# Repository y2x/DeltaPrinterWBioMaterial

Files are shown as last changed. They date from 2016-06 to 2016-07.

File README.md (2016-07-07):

# Delta 3D Printer With Bio-Material

## Video
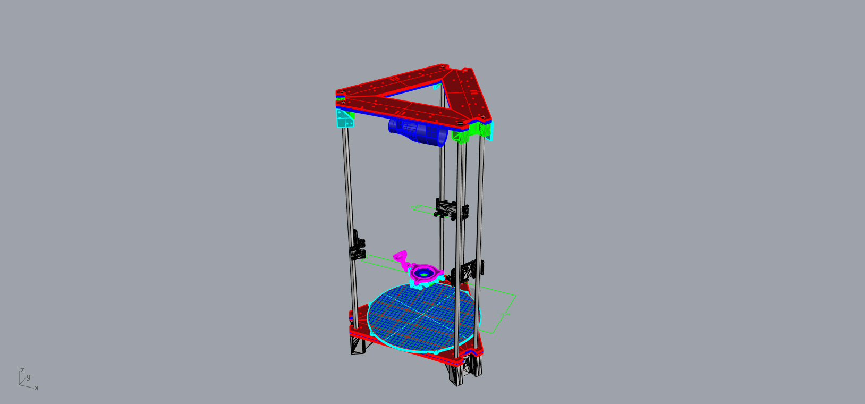
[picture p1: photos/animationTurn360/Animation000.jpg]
IMAGE ALT TEXT (https://youtu.be/-XNRGnteBmc)


## Description
This project is the continuation of Lorizio's :  *[`https://github.com/Lorizio/Delta-3D-Printer`](https://github.com/Lorizio/Delta-3D-Printer)*.
The main goal was to improve his existing printer and to be able to print different structures with home made materials.

## Construction
### Printed pieces :
- carriage : *[`http://www.thingiverse.com/thing:80425`](http://www.thingiverse.com/thing:80425)*
- idler end : *[`http://www.thingiverse.com/thing:143186`](http://www.thingiverse.com/thing:143186)*
- motor end : *[`http://www.thingiverse.com/thing:71687`](http://www.thingiverse.com/thing:71687)*
- platform : *[`http://www.thingiverse.com/thing:32850`](http://www.thingiverse.com/thing:32850)*
- ventilation : 
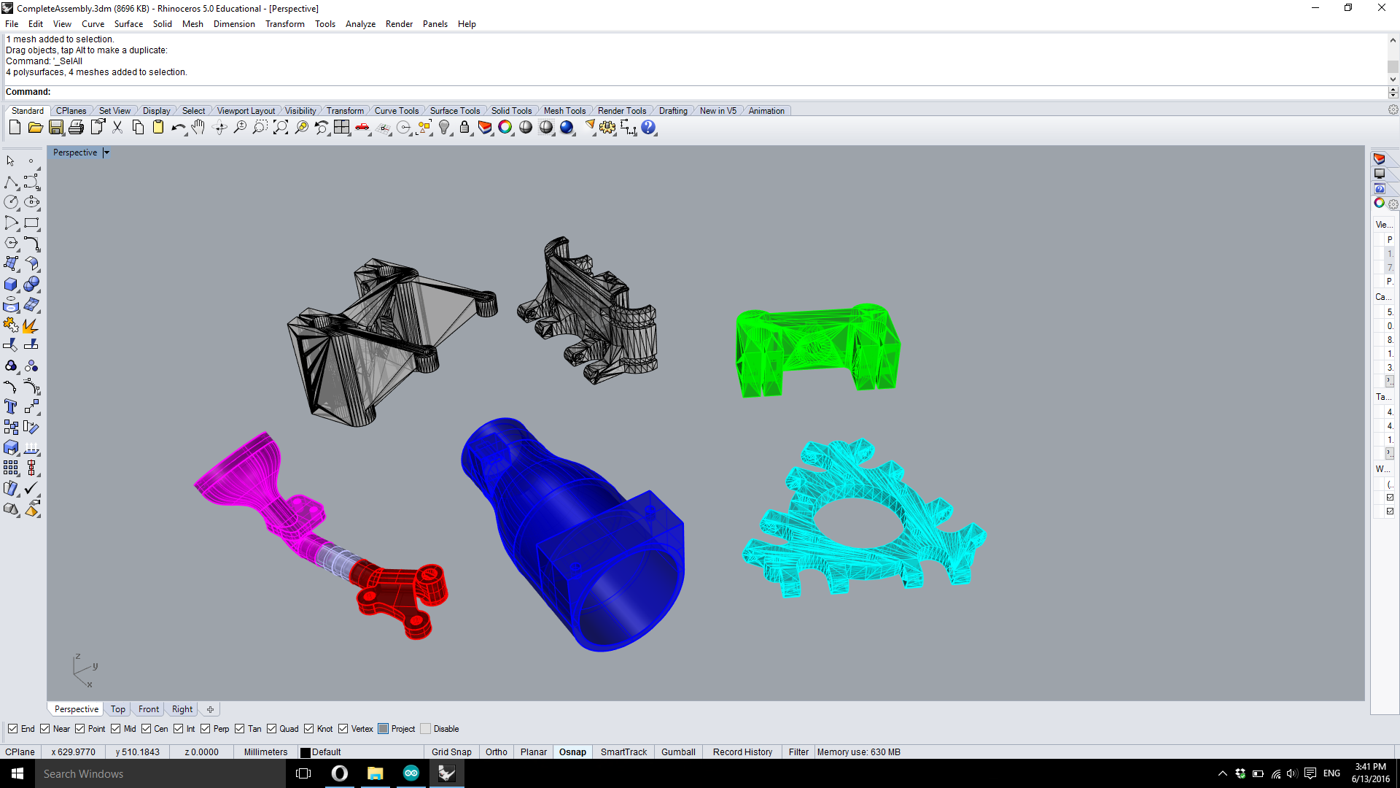
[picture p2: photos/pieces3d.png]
Printed pieces


### Laser-cut pieces for the frame:
- [Base assembly](hardware/baseAssembly.3dm)
- [Middle assembly](hardware/middleAssembly.3dm)
- [Top assembly](hardware/topAssembly.3dm)
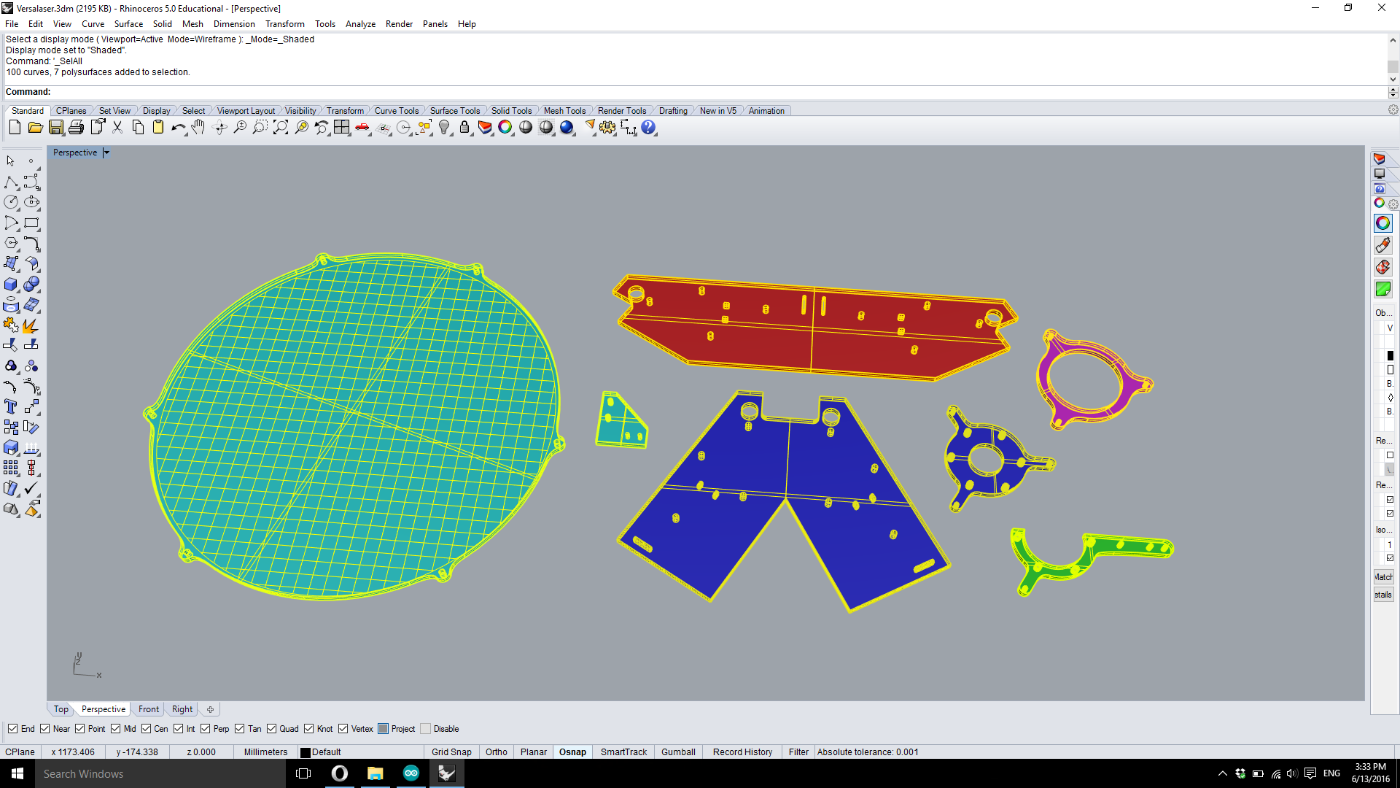
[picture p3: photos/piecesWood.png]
Wooden pieces


### Electronics & guiding
- [See the list](hardware/partsListToBuy.odt)

## Software & programs
### Arduino board
The actual prototype uses the [Marlin Firmware](https://github.com/MarlinFirmware/Marlin) which is widely used for custom 3D printer. The specifications are located in the configuration file in the marlin folder.
Here are the important sizing values :
```
  // Center-to-center distance of the holes in the diagonal push rods.
  #define DELTA_DIAGONAL_ROD 220.0 // mm

  // Horizontal offset from middle of printer to smooth rod center.
  #define DELTA_SMOOTH_ROD_OFFSET 178.0 // mm

  // Horizontal offset of the universal joints on the end effector.
  #define DELTA_EFFECTOR_OFFSET 33.5 // mm

  // Horizontal offset of the universal joints on the carriages.
  #define DELTA_CARRIAGE_OFFSET 28.0 // mm

  // Print surface diameter/2 minus unreachable space (avoid collisions with vertical towers).
  #define DELTA_PRINTABLE_RADIUS 90.0
```

### Slicer
The slicer was implemented using [Grasshopper3D](http://www.grasshopper3d.com/) on [Rhino3D](http://www.rhino3d.com/). It generates point from (almost) any brep surface and applies different transformations to the models to print interesting structures. Main features are to add zigzags (horizontally and vertically) change the layer height and the speed.
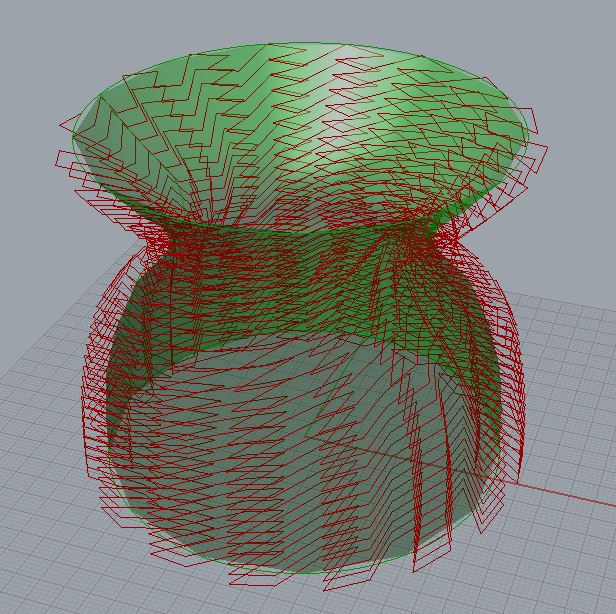
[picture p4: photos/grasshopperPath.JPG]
model in green, generated path in red


### Printed results
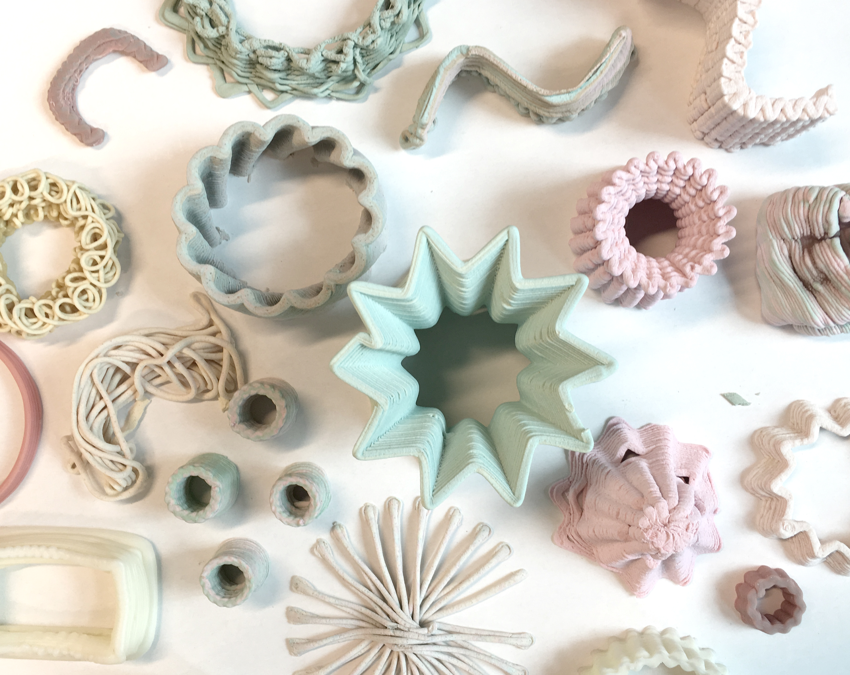
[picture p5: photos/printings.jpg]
printed results


### Authors
* **Philippe Heer** - *IC Master student*
* **Leonardo Wirz** - *IC Bachelor student*
* **Yuan Wang-Shih** - *Supervisor*
* **Huang Jeffrey** - *Professor*

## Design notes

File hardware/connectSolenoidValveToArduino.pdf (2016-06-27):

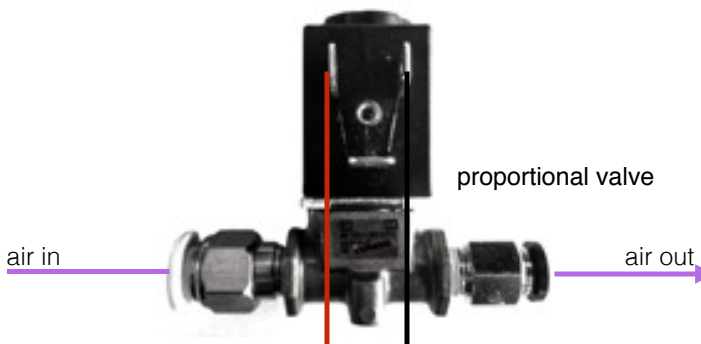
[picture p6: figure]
proportional valve; air in; air out
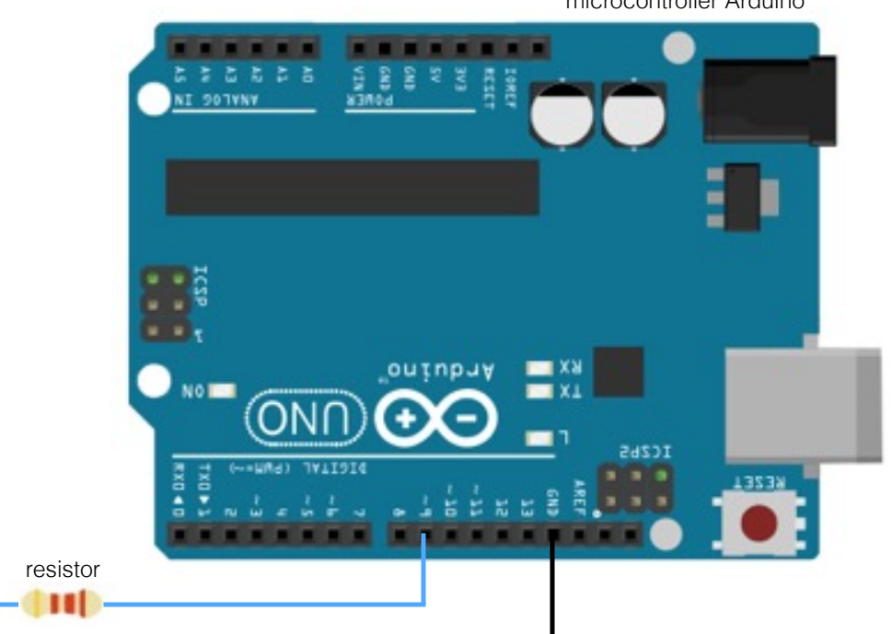
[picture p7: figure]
resistor

microcontroller Arduino

24V +

24V -

transistor

diode

#define valvePin 9

void setup() {
// put your setup code here, to run once: pinMode(valvePin, OUTPUT);

}

void loop() {

// put your main code here, to run repeatedly: analogWrite(valvePin, 170);
delay(15);

}

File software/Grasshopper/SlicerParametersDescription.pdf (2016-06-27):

Slicer parameters description

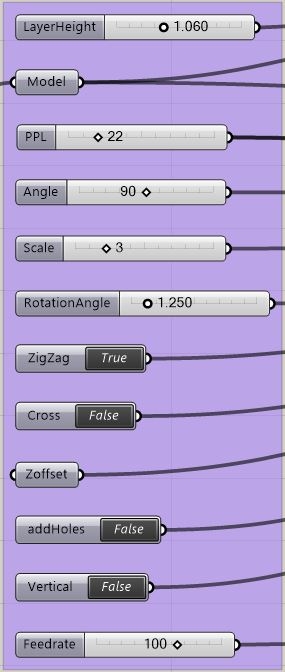
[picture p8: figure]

LayerHeight : set the layer height in millimeters between 0.5 and 2.

PPL : set the numbers of points per layers.

Angle : change the angle for the zigzag and crossed zigzag.

Scale : multiply the length of each line of the zigzag.

Rotation angle : twist the object, every layer rotates that angle in degrees.

ZigZag : enable zigzag.

Cross : enable crossed zigzag (only if zigzag is enabled).

Zoffset : shift the object in the z axis in millimeters.

AddHoles : removes certain points to create the hole effect.

Vertical : add a vetical zigzag.

Feedrate : set the speed printing, 60 = 1mm/s

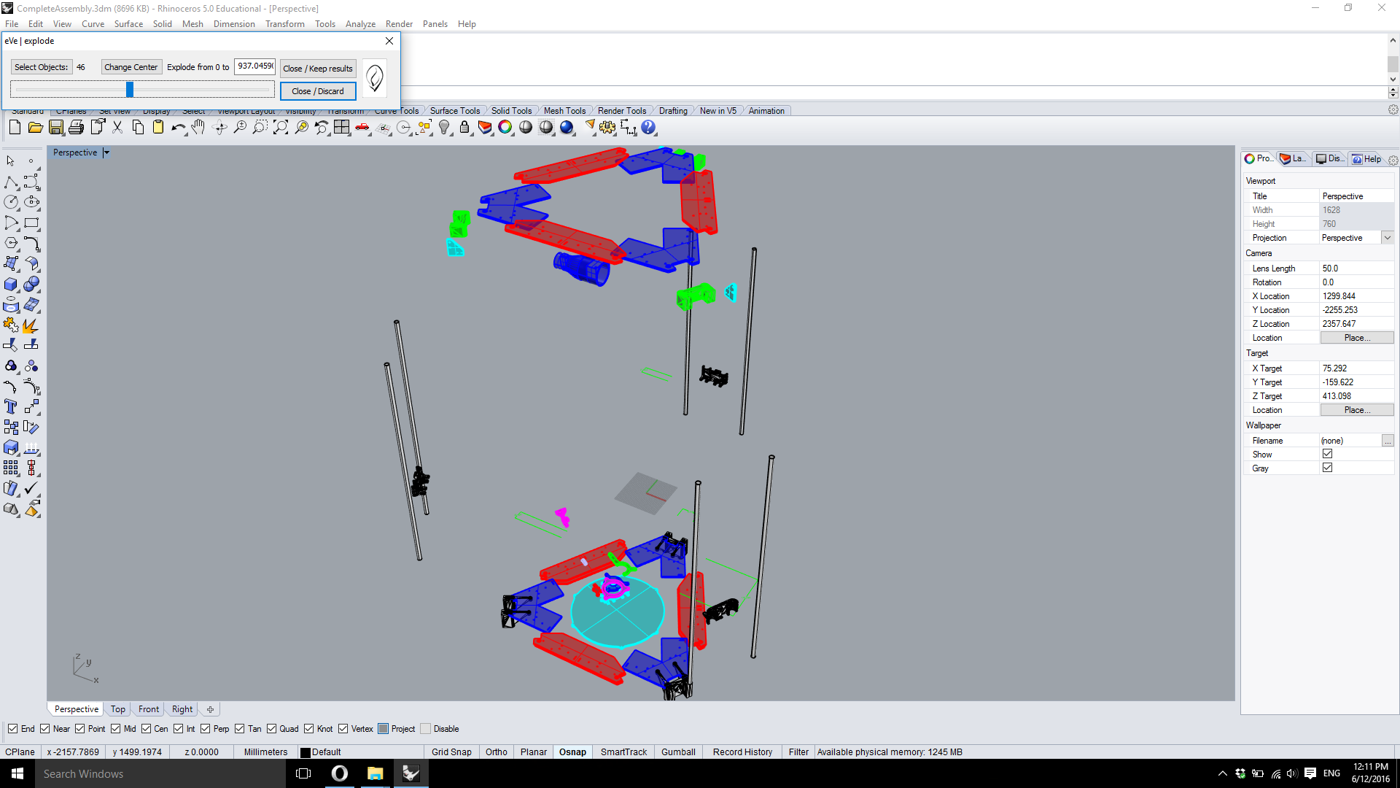
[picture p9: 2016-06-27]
photos/animationExplode/Screenshot (27).png

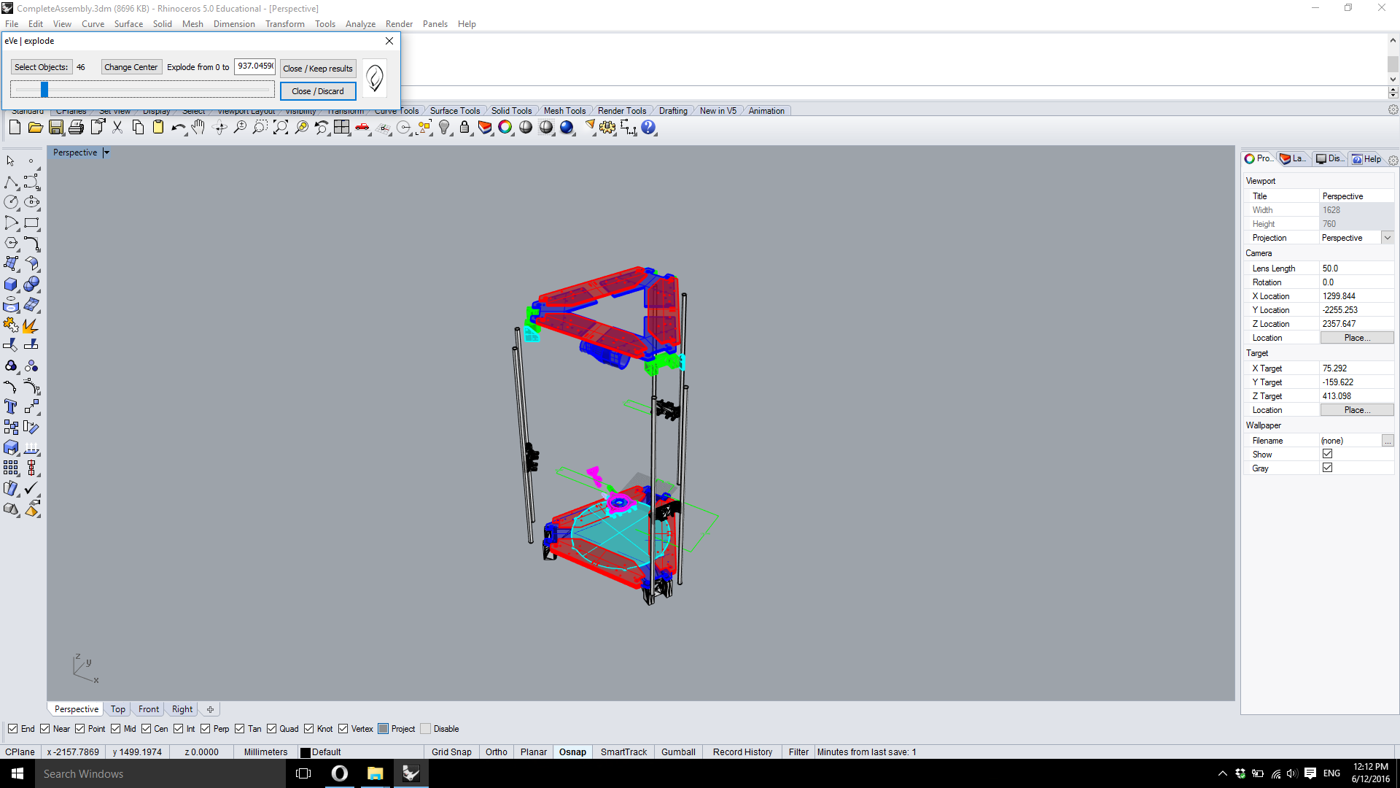
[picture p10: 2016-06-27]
photos/animationExplode/Screenshot (62).png

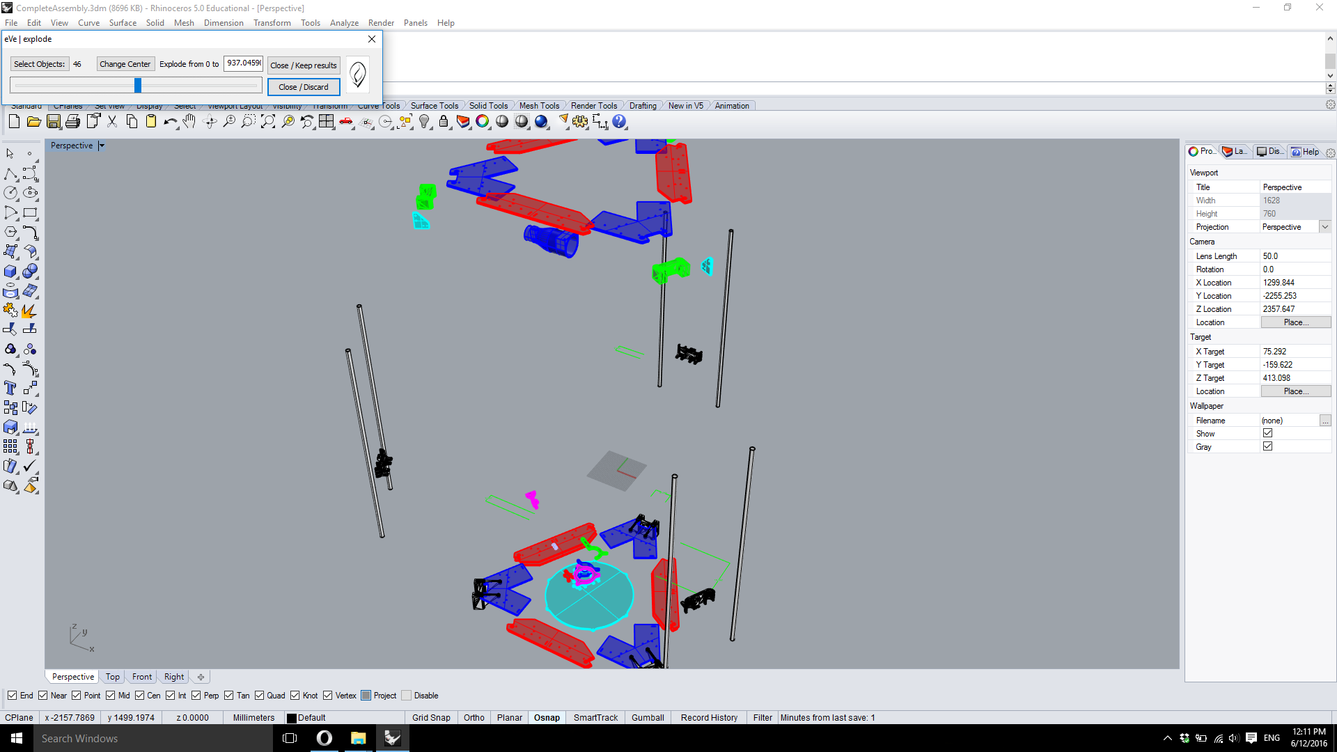
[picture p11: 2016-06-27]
photos/animationExplode/Screenshot (21).png

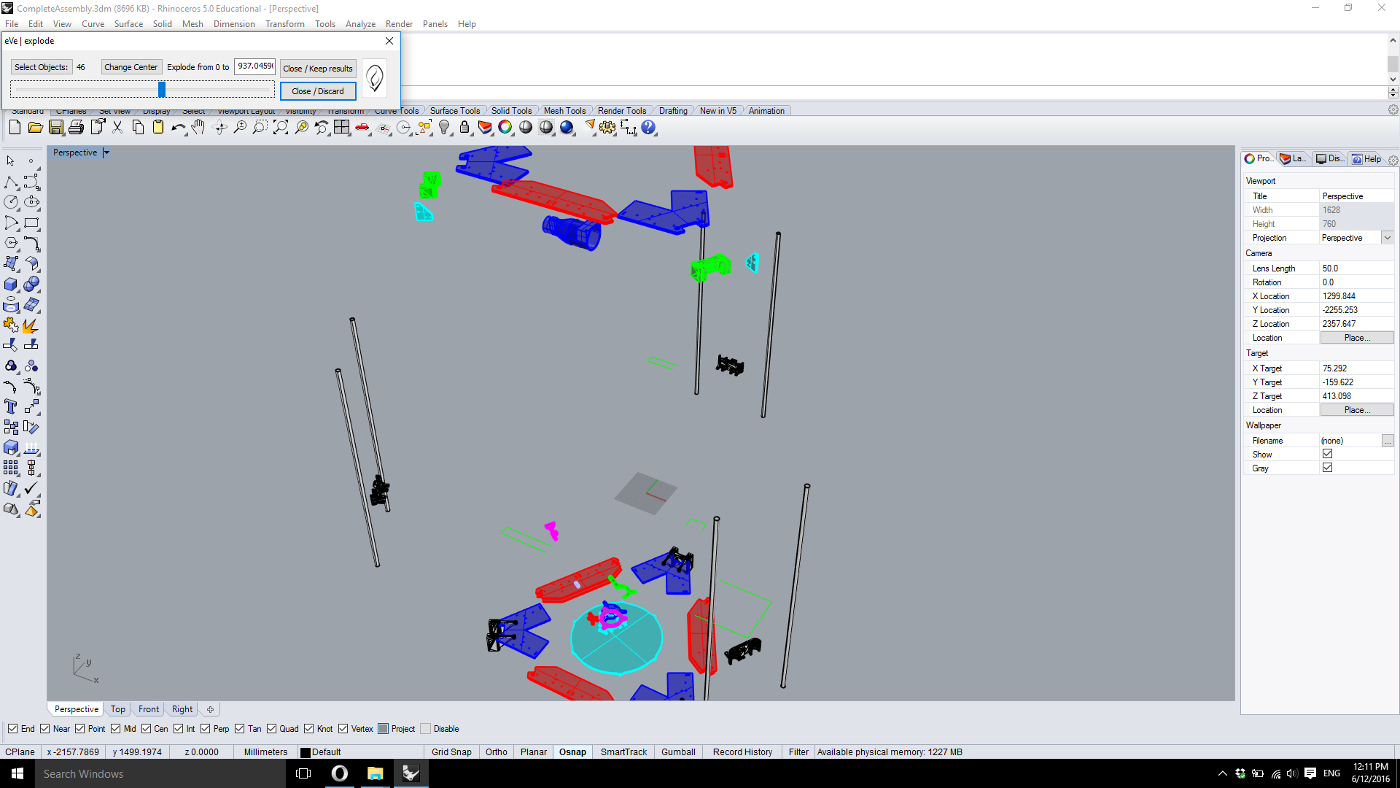
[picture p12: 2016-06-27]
photos/animationExplode/Screenshot (14).png

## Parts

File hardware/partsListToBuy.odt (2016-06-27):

You will need an air compressor machine accurate enough to control the pressure efficiently.

Structure parts :

High torque hybrid (3x)

http://www.zappautomation.co.uk/sy42sth47-1684a-high-torque-hybrid-stepper-motors.html

12mm steel rods (6x)

http://www.zappautomation.co.uk/sfc12-precision-round-rail.html

12 mm linear bearing (6x)

They need to slide along the steel rods smoothly

http://www.zappautomation.co.uk/lm10uu-linear-bearing-29451.html

GT2 belts (3x)

http://www.amazon.com/3DMakerWorld-GT2-Timing-Belt/dp/B00IDCG6ZU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

Traxxas 5347 with hollows balls (12x)

They must fit in the brass tube below. Two per tube.

http://www.amazon.com/Traxxas-5347-Hollow-Balls-Large/dp/B000BOLVJY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

Brass tube 8mm (6x)

Two tubes per axis. 23 centimeters each. The material doesn’t matter as long as it is solid and that the traxxas pieces can fit inside.

http://www.amazon.com/Engineering-Round-Brass-Tube-45/dp/B005WPASOG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

xbox 360 203W power brick 220V

http://www.amazon.co.uk/OFFICIAL-MICROSOFT-REPLACEMENT-POWER-SUPPLY/dp/B00AUYDF6M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

Some MDF panels of at least 12 mm.

Electronic part

Ultra Set (1x)

It comes with wires and all the required electronic components

https://gadgets3d.eu/index.php?route=product/product&product_id=70

Extruder parts

Glue Liquid Cartridge Dispenser Syringe Barrel 300CC Clear Black

http://www.amazon.co.uk/Liquid-Cartridge-Dispenser-Syringe-Barrel/dp/B00GMW4EBG

tips

http://www.adhesivedispensers.co.uk/TE714025PK.htm

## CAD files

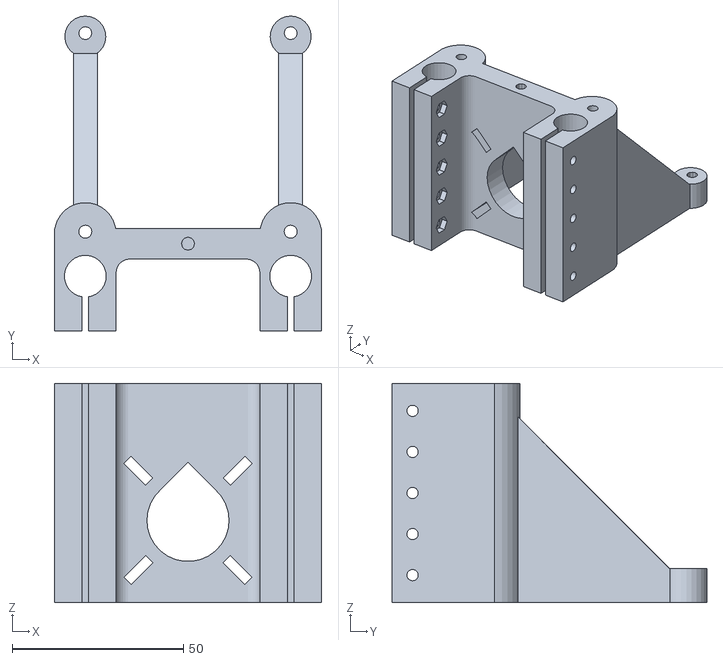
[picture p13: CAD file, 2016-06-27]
hardware/motor_end.stl
78.0 x 92.0 x 64.0

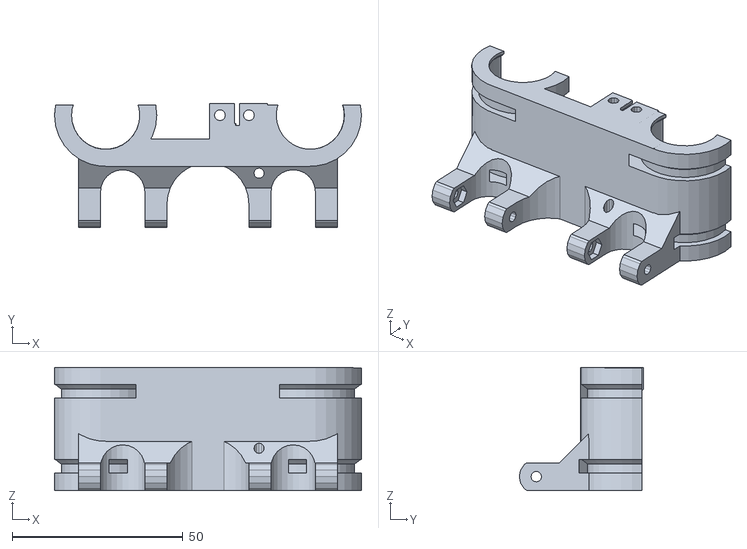
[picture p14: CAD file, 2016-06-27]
hardware/carriage-V1.2.stl
90.0 x 36.5 x 36.1

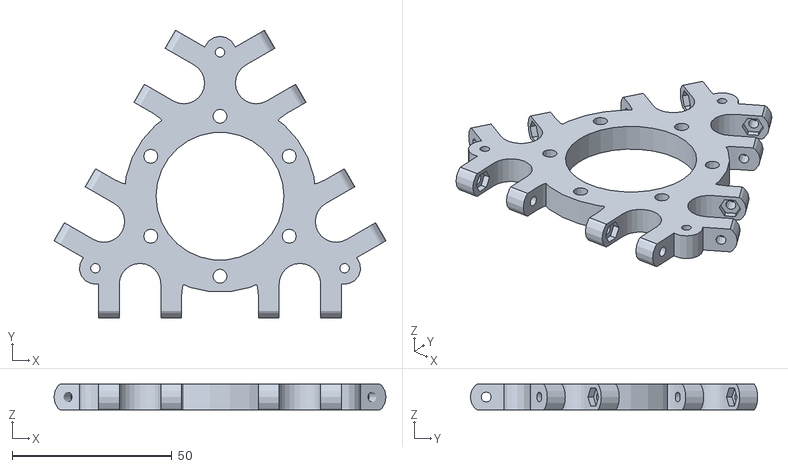
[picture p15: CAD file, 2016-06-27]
hardware/platform.stl
103.8 x 89.9 x 8.00

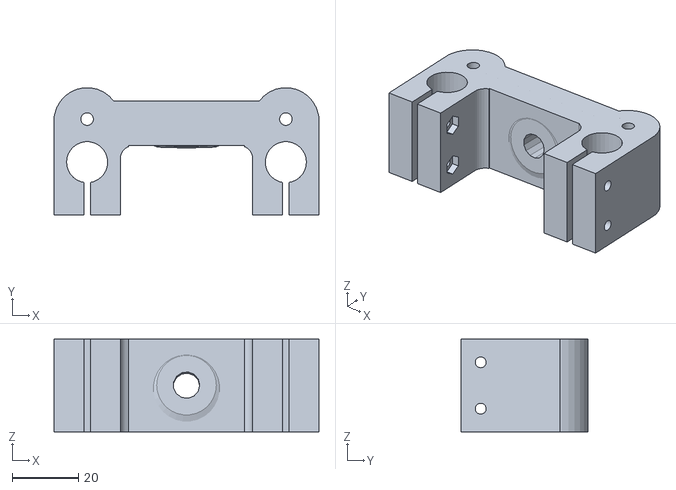
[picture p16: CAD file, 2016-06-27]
hardware/idler_end_V1.2.stl
80.0 x 38.4 x 28.0

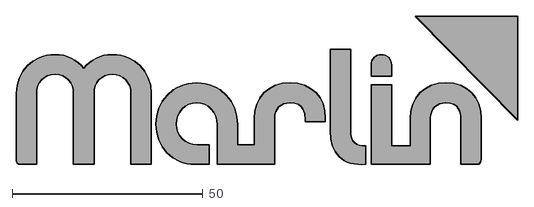
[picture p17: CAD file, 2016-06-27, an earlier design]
software/Arduino/Marlin-RC/Documentation/Logo/Marlin Logo_old.dxf
131.6 x 39.5

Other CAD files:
hardware/baseAssembly.3dm
hardware/middleAssembly.3dm
hardware/topAssembly.3dm

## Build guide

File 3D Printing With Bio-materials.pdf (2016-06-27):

by L. Wirz, P. Heer
Supervisor Y. Wang
Professor J. Huang

## 3D Printing With Bio-materials

### Outline

- Goal
- Hardware
- Software
- Material
- Issues

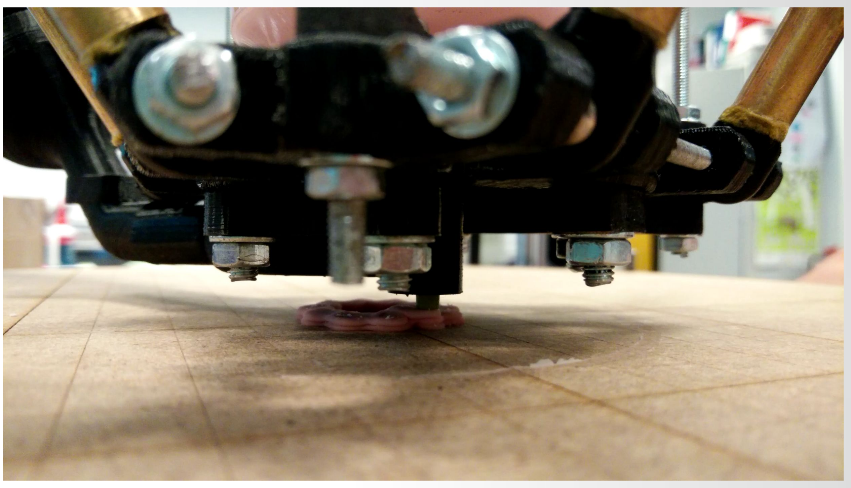
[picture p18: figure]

- Further development
- Demo

### Goal

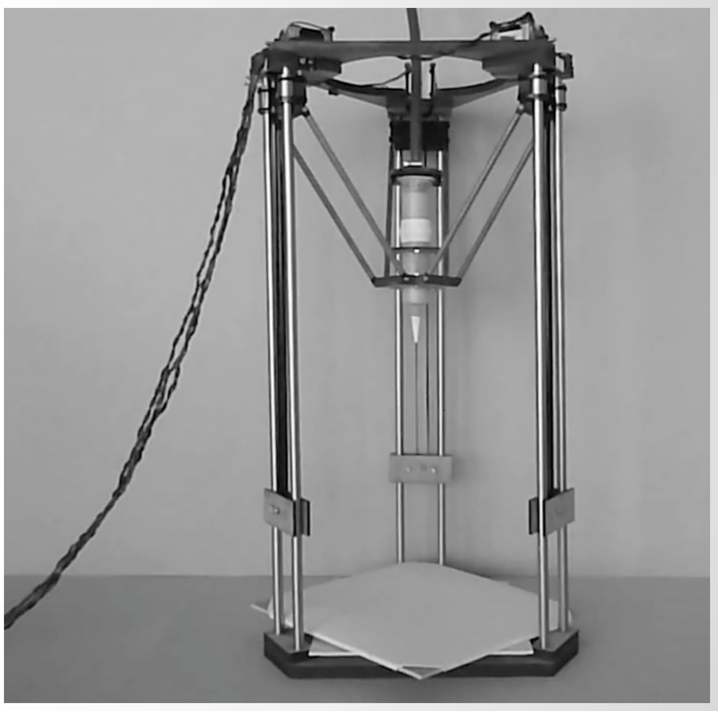
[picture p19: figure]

- improve existing printer
- new materials
- print different textures

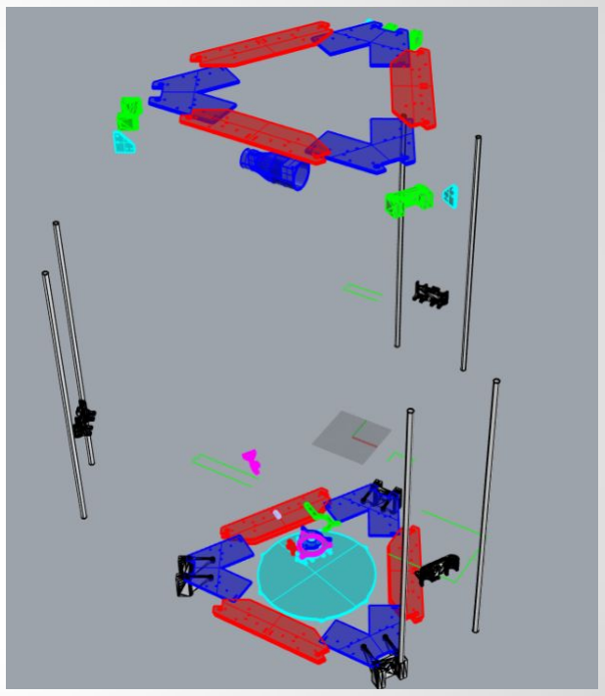
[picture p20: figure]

### Hardware

- Motors and sensors
- Air compressor
- Design with Rhino 5.0
- Cut with Versalaser
- Print with Makerbot Mini

### Wooden pieces

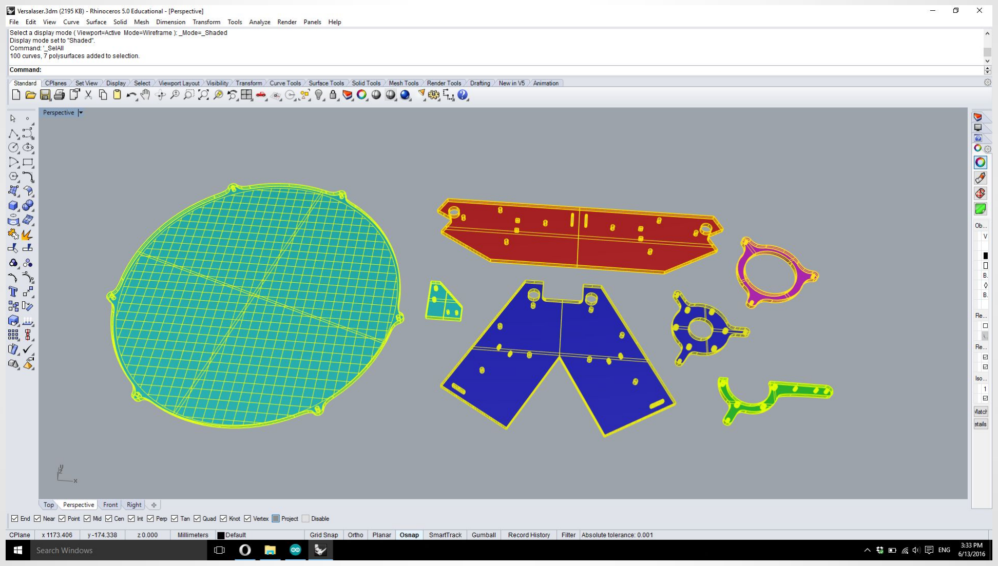
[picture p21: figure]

### 3d printed pieces

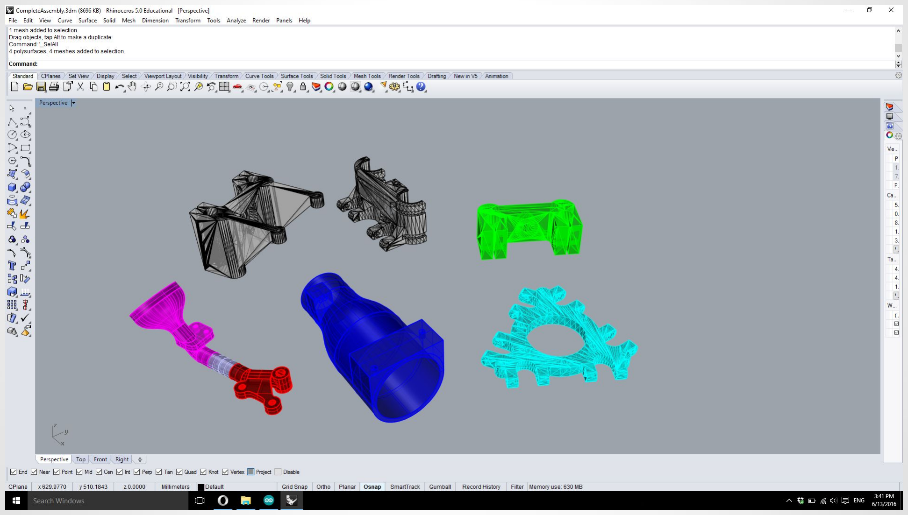
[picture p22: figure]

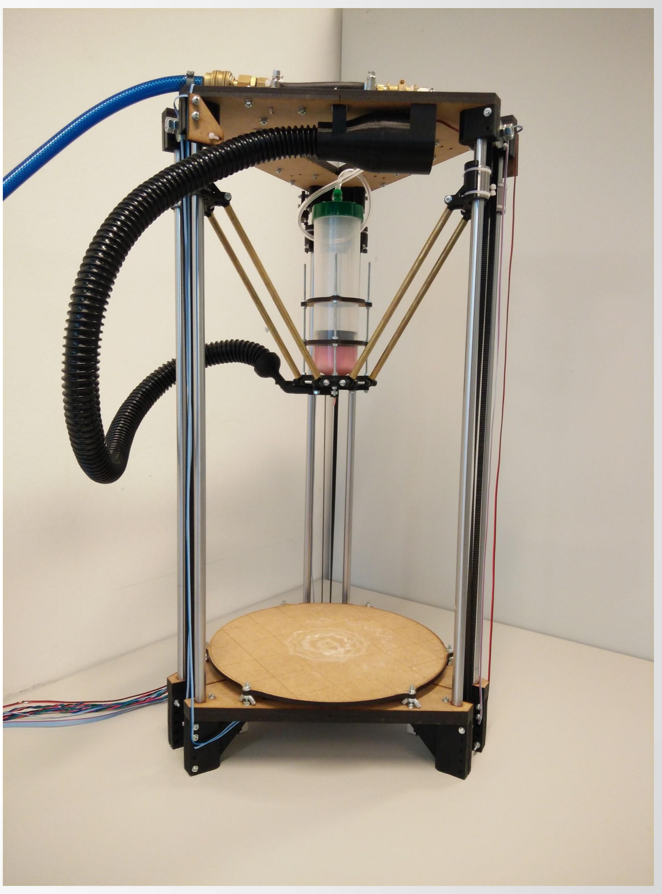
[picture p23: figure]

### Specifications

- diameter: 18cm
- height: 31cm
- speed: 1-2mm/s
- precision: 0.2mm
- pressure: 4 bar

### Material

- 100ml glue, 100g Maizena
- 4 spoons flour, 2 or 1 spoons salt and some water
- Food coloring

### Software

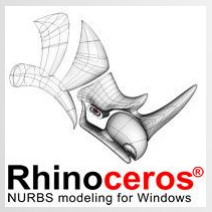
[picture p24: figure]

- Rhino 5.0

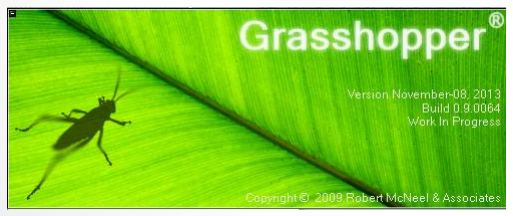
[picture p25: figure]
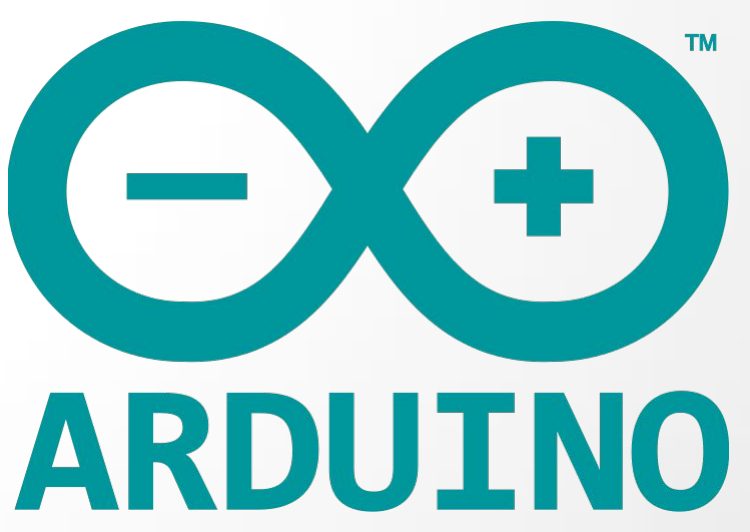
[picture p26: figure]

- Grasshopper (plugin of Rhino)
- Arduino Marlin RC software

### Custom slicer

- Create different paths and textures
- Zigzag (horizontal / vertical / alternating / angle)
- Speed variable
- Layer height, layer offset

### Slicer interface

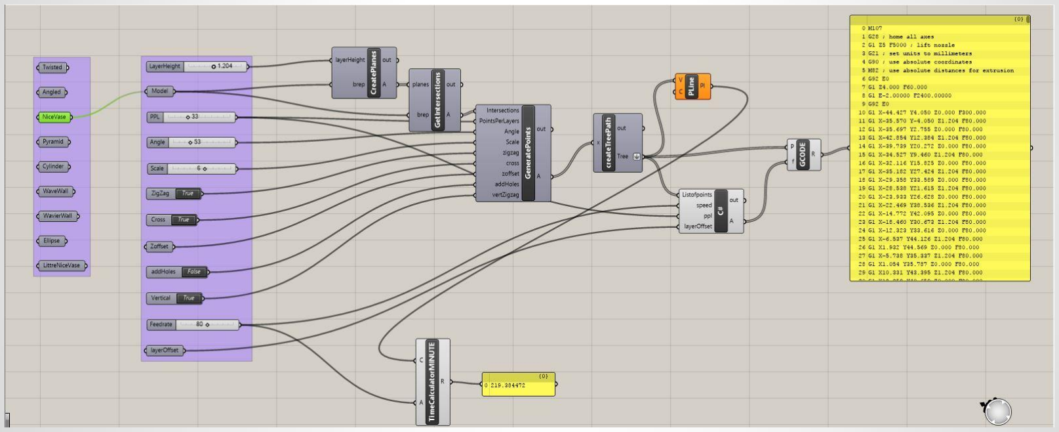
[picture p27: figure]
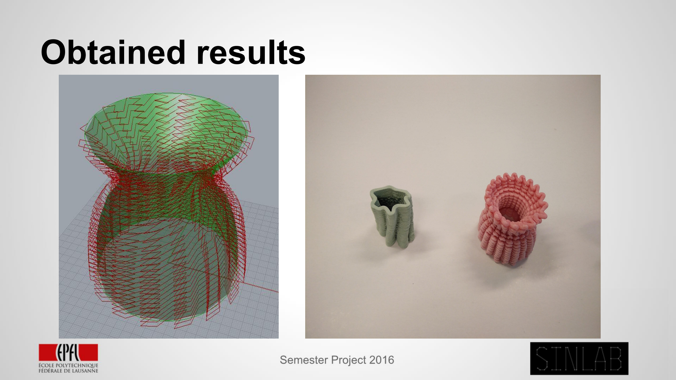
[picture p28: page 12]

### Obtained results

### Issues

- Makerbot Mini
- Printer calibration
- Material (2 different recipes)
- Printtime

### Further development

- Use other extruders
- Other materials

### Demo

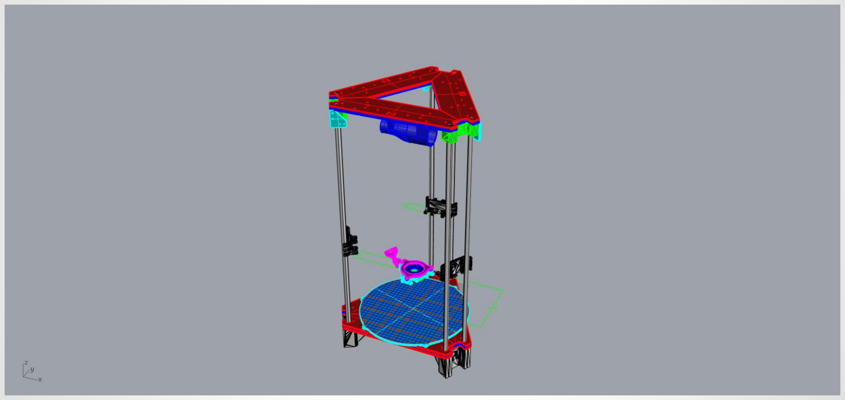
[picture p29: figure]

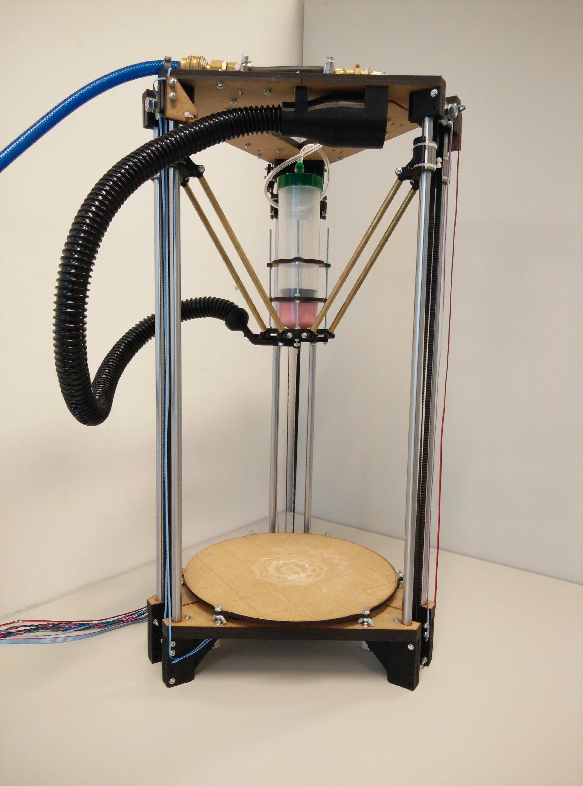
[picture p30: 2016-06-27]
photos/deltaPrinter.jpg

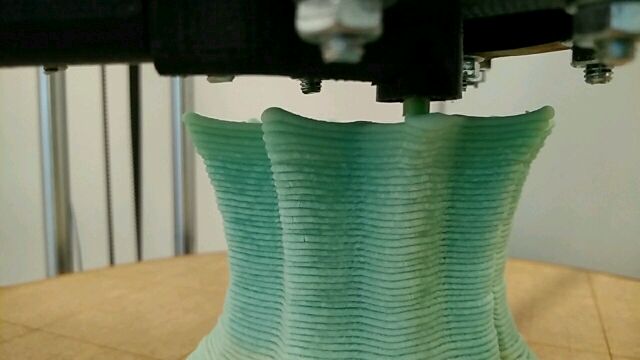
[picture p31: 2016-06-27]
photos/printing2.jpg

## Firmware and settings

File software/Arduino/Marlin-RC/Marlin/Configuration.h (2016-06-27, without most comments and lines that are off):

#define CONFIGURATION_H
#include "boards.h"
#include "macros.h"
#if ENABLED(USE_AUTOMATIC_VERSIONING)
  #include "_Version.h"
#else
  #include "Version.h"
#endif
#define STRING_CONFIG_H_AUTHOR "(none, default config)" // Who made the changes.
#define SHOW_BOOTSCREEN
#define STRING_SPLASH_LINE1 SHORT_BUILD_VERSION // will be shown during bootup in line 1
#define SERIAL_PORT 0
#define BAUDRATE 250000
  #define MOTHERBOARD BOARD_RAMPS_13_EFB
#define CUSTOM_MACHINE_NAME "DeltaSinlab"
#define EXTRUDERS 1
#define POWER_SUPPLY 1
#define TEMP_SENSOR_0 2
#define TEMP_SENSOR_1 0
#define TEMP_SENSOR_2 0
#define TEMP_SENSOR_3 0
#define TEMP_SENSOR_BED 0
#define MAX_REDUNDANT_TEMP_SENSOR_DIFF 10
#define TEMP_RESIDENCY_TIME 10  // (seconds)
#define TEMP_HYSTERESIS 3       // (degC) range of +/- temperatures considered "close" to the target one
#define TEMP_WINDOW     1       // (degC) Window around target to start the residency timer x degC early.
#define TEMP_BED_RESIDENCY_TIME 0   // (seconds)
#define TEMP_BED_HYSTERESIS 3       // (degC) range of +/- temperatures considered "close" to the target one
#define TEMP_BED_WINDOW     1       // (degC) Window around target to start the residency timer x degC early.
#define HEATER_0_MINTEMP 5
#define HEATER_1_MINTEMP 5
#define HEATER_2_MINTEMP 5
#define HEATER_3_MINTEMP 5
#define BED_MINTEMP 5
#define HEATER_0_MAXTEMP 2750
#define HEATER_1_MAXTEMP 275
#define HEATER_2_MAXTEMP 275
#define HEATER_3_MAXTEMP 275
#define BED_MAXTEMP 150
#define PIDTEMP
#define BANG_MAX 255 // limits current to nozzle while in bang-bang mode; 255=full current
#define PID_MAX BANG_MAX // limits current to nozzle while PID is active (see PID_FUNCTIONAL_RANGE below); 255=full current
  #define PID_FUNCTIONAL_RANGE 10 // If the temperature difference between the target temperature and the actual temperature
  #define PID_INTEGRAL_DRIVE_MAX PID_MAX  //limit for the integral term
  #define K1 0.95 //smoothing factor within the PID
  #define  DEFAULT_Kp 22.2
  #define  DEFAULT_Ki 1.08
  #define  DEFAULT_Kd 114
#define MAX_BED_POWER 255 // limits duty cycle to bed; 255=full current
#define PREVENT_DANGEROUS_EXTRUDE
#define PREVENT_LENGTHY_EXTRUDE
#define EXTRUDE_MINTEMP 170
#define EXTRUDE_MAXLENGTH (X_MAX_LENGTH+Y_MAX_LENGTH) //prevent extrusion of very large distances.
#define THERMAL_PROTECTION_HOTENDS // Enable thermal protection for all extruders
#define THERMAL_PROTECTION_BED     // Enable thermal protection for the heated bed
#define DELTA
  #define DELTA_SEGMENTS_PER_SECOND 100
  #define DELTA_DIAGONAL_ROD 220.0 // mm
  #define DELTA_SMOOTH_ROD_OFFSET 178.0 // mm
  #define DELTA_EFFECTOR_OFFSET 33.5 // mm
  #define DELTA_CARRIAGE_OFFSET 28.0 // mm
  #define DELTA_RADIUS (DELTA_SMOOTH_ROD_OFFSET-(DELTA_EFFECTOR_OFFSET)-(DELTA_CARRIAGE_OFFSET))
  #define DELTA_PRINTABLE_RADIUS 90.0
#define USE_XMAX_PLUG
#define USE_YMAX_PLUG
#define USE_ZMAX_PLUG
#define ENDSTOPPULLUPS // Comment this out (using // at the start of the line) to disable the endstop pullup resistors
const bool X_MIN_ENDSTOP_INVERTING = false; // set to true to invert the logic of the endstop.
const bool Y_MIN_ENDSTOP_INVERTING = false; // set to true to invert the logic of the endstop.
const bool Z_MIN_ENDSTOP_INVERTING = false; // set to true to invert the logic of the endstop.
const bool X_MAX_ENDSTOP_INVERTING = false; // set to true to invert the logic of the endstop.
const bool Y_MAX_ENDSTOP_INVERTING = false; // set to true to invert the logic of the endstop.
const bool Z_MAX_ENDSTOP_INVERTING = false; // set to true to invert the logic of the endstop.
const bool Z_MIN_PROBE_ENDSTOP_INVERTING = true; // set to true to invert the logic of the endstop.
#define X_ENABLE_ON 0
#define Y_ENABLE_ON 0
#define Z_ENABLE_ON 0
#define E_ENABLE_ON 0 // For all extruders
#define DISABLE_X false
#define DISABLE_Y false
#define DISABLE_Z false
#define DISABLE_E false // For all extruders
#define DISABLE_INACTIVE_EXTRUDER true //disable only inactive extruders and keep active extruder enabled
#define INVERT_X_DIR false // DELTA does not invert
#define INVERT_Y_DIR false
#define INVERT_Z_DIR false
#define INVERT_E0_DIR false
#define INVERT_E1_DIR false
#define INVERT_E2_DIR false
#define INVERT_E3_DIR false
#define X_HOME_DIR 1  // deltas always home to max
#define Y_HOME_DIR 1
#define Z_HOME_DIR 1
#define min_software_endstops true // If true, axis won't move to coordinates less than HOME_POS.
#define max_software_endstops true  // If true, axis won't move to coordinates greater than the defined lengths below.
#define X_MIN_POS -(DELTA_PRINTABLE_RADIUS)
#define Y_MIN_POS -(DELTA_PRINTABLE_RADIUS)
#define Z_MIN_POS 0
#define X_MAX_POS DELTA_PRINTABLE_RADIUS
#define Y_MAX_POS DELTA_PRINTABLE_RADIUS
#define Z_MAX_POS MANUAL_Z_HOME_POS
#define MANUAL_HOME_POSITIONS  // If defined, MANUAL_*_HOME_POS below will be used
  #define MANUAL_X_HOME_POS 0
  #define MANUAL_Y_HOME_POS 0
  #define MANUAL_Z_HOME_POS 309 // For delta: Distance between nozzle and print surface after homing.
#define HOMING_FEEDRATE_XYZ (60*60)
#define HOMING_FEEDRATE_E 0
#define HOMING_FEEDRATE { HOMING_FEEDRATE_XYZ, HOMING_FEEDRATE_XYZ, HOMING_FEEDRATE_XYZ, HOMING_FEEDRATE_E }
#define DEFAULT_AXIS_STEPS_PER_UNIT   {80, 80, 80, 760*1.1}  // default steps per unit for Kossel (GT2, 20 tooth)
#define DEFAULT_MAX_FEEDRATE          {500, 500, 500, 25}    // (mm/sec)
#define DEFAULT_MAX_ACCELERATION      {2000,2000,2000,10000}    // X, Y, Z, E maximum start speed for accelerated moves. E default values are good for Skeinforge 40+, for older versions raise them a lot.
#define DEFAULT_ACCELERATION          3000    // X, Y, Z and E acceleration in mm/s^2 for printing moves
#define DEFAULT_RETRACT_ACCELERATION  3000    // E acceleration in mm/s^2 for retracts
#define DEFAULT_TRAVEL_ACCELERATION   3000    // X, Y, Z acceleration in mm/s^2 for travel (non printing) moves
#define DEFAULT_XYJERK                20.0    // (mm/sec)
#define DEFAULT_ZJERK                 20.0    // (mm/sec) Must be same as XY for delta
#define DEFAULT_EJERK                 5.0     // (mm/sec)
#define CUSTOM_M_CODES
  #define DEFAULT_KEEPALIVE_INTERVAL 2 // Number of seconds between "busy" messages. Set with M113.
#define PLA_PREHEAT_HOTEND_TEMP 180
#define PLA_PREHEAT_HPB_TEMP 70
#define PLA_PREHEAT_FAN_SPEED 255   // Insert Value between 0 and 255
#define ABS_PREHEAT_HOTEND_TEMP 240
#define ABS_PREHEAT_HPB_TEMP 100
#define ABS_PREHEAT_FAN_SPEED 255   // Insert Value between 0 and 255
#define LANGUAGE_INCLUDE GENERATE_LANGUAGE_INCLUDE(en)
#define DISPLAY_CHARSET_HD44780_JAPAN        // this is the most common hardware
#define SDSUPPORT
#define ULTIMAKERCONTROLLER
#define SOFT_PWM_SCALE 0
#define DEFAULT_NOMINAL_FILAMENT_DIA 3.00  //Enter the diameter (in mm) of the filament generally used (3.0 mm or 1.75 mm) - this is then used in the slicer software.  Used for sensor reading validation
#include "Configuration_adv.h"
#include "thermistortables.h"

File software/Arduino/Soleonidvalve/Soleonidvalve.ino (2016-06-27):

int valvePin = 3;

void setup() {
  // put your setup code here, to run once:
  //Serial.begin(9600);
  pinMode(valvePin, OUTPUT);
}

void loop() {
//  put your main code here, to run repeatedly:
 //if(Serial.available() > 0){
  
   //static int v = Serial.read();
   analogWrite(valvePin, 255);
 //}
  //Serial.flush();
} 

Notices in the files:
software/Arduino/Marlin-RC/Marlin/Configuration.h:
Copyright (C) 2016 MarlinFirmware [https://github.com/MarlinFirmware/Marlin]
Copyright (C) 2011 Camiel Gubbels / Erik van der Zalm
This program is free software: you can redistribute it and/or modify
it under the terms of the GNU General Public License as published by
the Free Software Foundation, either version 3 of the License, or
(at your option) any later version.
